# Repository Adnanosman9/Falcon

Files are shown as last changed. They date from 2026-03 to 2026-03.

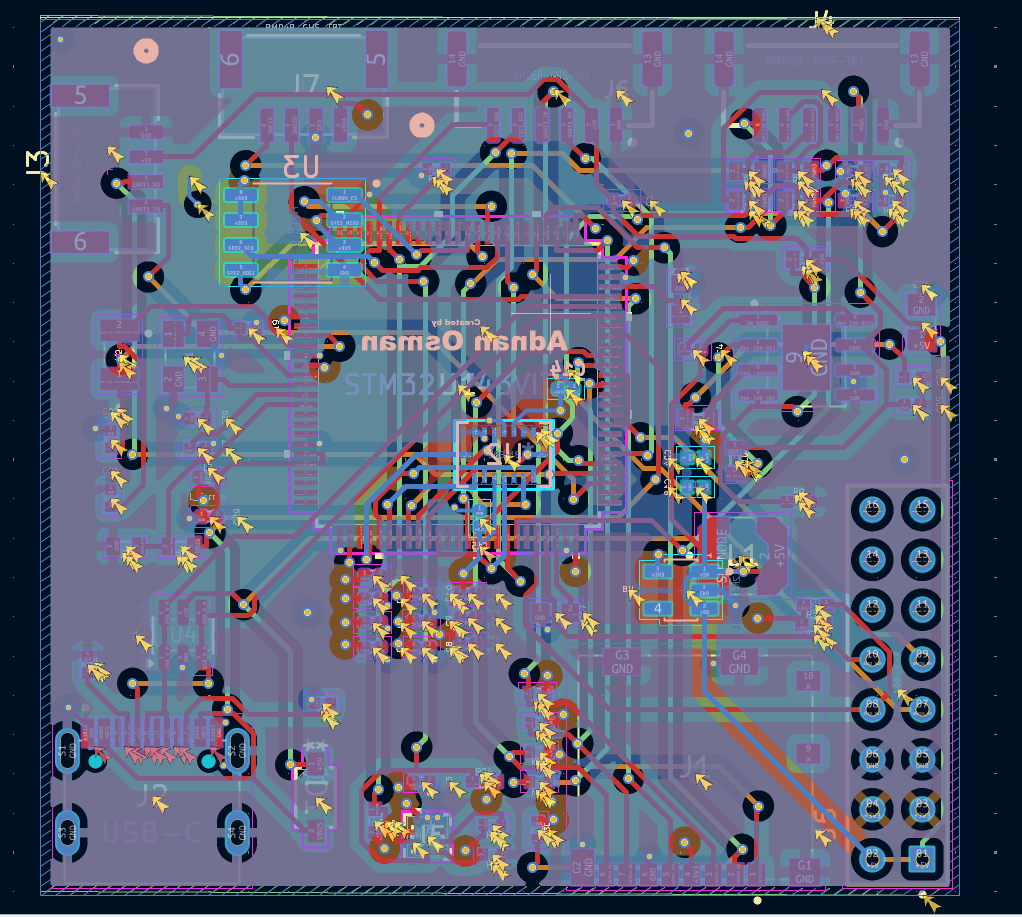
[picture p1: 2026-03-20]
Images/Screenshot 2026-03-19 203201.png

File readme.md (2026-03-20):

<h1 align="center">
  Falcon
  <br>
</h1>

<h4 align="center">
A custom flight controller built from scratch for a 3D surveying drone, running a custom port of ArduPilot
</h4>

<div align="center">





</div>

## Overview

I wanted to build a drone that could do proper 3D photogrammetry surveys. Off-the-shelf F4 flight controllers don't have enough processing power for the EKF configuration I need when fusing RTK GPS with IMU data at high rates. So I designed my own.

This is a flight controller built around the **STM32H743VIT6** , a 480MHz Cortex-M7 chip with 2MB flash and 1MB RAM. It runs a custom-compiled ArduPilot firmware with pin mappings specific to this board.

> ⚠️ PCB has not been manufactured yet. Firmware compiles and is ready to flash, but nothing has been tested on real hardware.

---

## Hardware Specs

| Component | Part |
| :--- | :--- |
| MCU | STM32H743VIT6 (480MHz, 2MB Flash) |
| IMU | BMI088 (6-axis, vibration-robust) |
| Barometer | BMP390 |
| Magnetometer | BMM350 |
| Flash Logging | FM25V02A (256KB FRAM) |
| SD Card | SDMMC1 4-bit interface |
| Power Input | MP1584EN buck → LP5907 3.3V LDO |
| USB | USB-C with USBLC6-2SC6 ESD protection |

---

## Why I Built It

I wanted to understand how flight controllers actually work, not just use one. Designing the schematic, figuring out why the VCAP pins need specific 2.2µF caps, getting the crystal load capacitors right, debugging the ArduPilot hwdef syntax , all of that taught me things I wouldn't have learned any other way.

Also, most hobbyist FCs are F4-based. The H7 gives me enough headroom to run ArduPilot's EKF3 with RTK GPS fusion without the processor struggling.

---

## How I Built It

### Schematic (KiCad)
- Designed the full power tree: LiPo → MP1584EN (5V buck) → LP5907 (3.3V LDO)
- VCAP1 and VCAP2 need exactly 2.2µF ceramic caps or the STM32H7 internal LDO becomes unstable, took a while to figure that out
- USB-C CC pins need 5.1kΩ pull-downs to GND or no charger recognizes the board as a device

### PCB Layout (KiCad)
- 4-layer board with bottom copper GND pour
- Crystal section has an isolated GND island underneath to avoid noise coupling into the oscillator
- DRC ended with 9 warnings, all on USB-C pad spacing (DRC settings issue, not a real problem). Zero footprint errors.

### Firmware (ArduPilot)
- Created a custom `hwdef.dat` that maps all STM32 pins to physical components: SPI for BMI088, I2C for BMP390 and BMM350, SDMMC1 for SD card, USART3 for GPS, PWM on TIM1
- Had to build a custom ChibiOS bootloader before the main firmware would compile
- Built on WSL (Ubuntu) using the `waf` build system and `arm-none-eabi-gcc`

---

## Current Status

- ✅ Schematic complete
- ✅ PCB layout complete, DRC clean
- ✅ Custom ArduPilot firmware builds successfully
- ⏳ PCB not manufactured yet
- ⏳ Not tested on real hardware

---

## How to Build Firmware

```bash
git clone --recurse-submodules https://github.com/ArduPilot/ardupilot.git
cd ardupilot
Tools/environment_install/install-prereqs-ubuntu.sh -y
. ~/.profile
mkdir libraries/AP_HAL_ChibiOS/hwdef/H7-DroneFC
cp Firmware/hwdef.dat libraries/AP_HAL_ChibiOS/hwdef/H7-DroneFC/
python Tools/scripts/build_bootloaders.py H7-DroneFC
./waf configure --board=H7-DroneFC
./waf copter
```

Output: `build/H7-DroneFC/bin/arducopter.bin`

---

## How to Flash

Connect an **ST-Link V2** to the SWD header:

| Header Pin | Signal |
| :--- | :--- |
| 1 | +3V3 |
| 2 | SWDIO (PA13) |
| 3 | SWCLK (PA14) |
| 4 | GND |

Flash `arducopter.bin` using STM32CubeProgrammer or Mission Planner (Load custom firmware).

---

## PWM Motor Outputs

| Output | MCU Pin | Timer |
| :--- | :--- | :--- |
| Motor 1 | PE9 | TIM1_CH1 |
| Motor 2 | PE11 | TIM1_CH2 |
| Motor 3 | PE13 | TIM1_CH3 |
| Motor 4 | PE14 | TIM1_CH4 |

---

## Repository Structure

```
H7-DroneFC/
├── PCB/     # KiCad schematic (.kicad_sch) and PCB layout (.kicad_pcb)
├── Firmware/     # hwdef.dat for ArduPilot custom board build
└── Images/       # Schematic screenshots and PCB renders
```

---

## ⚠️ Caution

Firmware has not been tested on real hardware yet. There may be issues with sensor initialization, SPI timing, or I2C addresses that only show up on actual hardware. Double check all pin assignments against the schematic before flashing and expect some debugging on first boot.

---

## Credits

- [ArduPilot](https://ardupilot.org/) for the open-source flight stack
- [KiCad](https://www.kicad.org/) for PCB design
- [Hack Club](https://hackclub.com/) for support

---

> GitHub [@Adnanosman9](https://github.com/Adnanosman9)

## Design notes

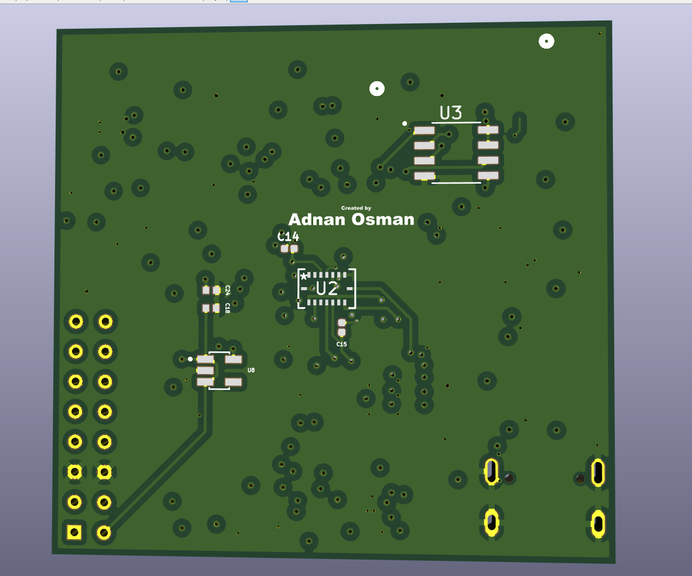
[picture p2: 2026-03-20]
Images/Screenshot 2026-03-19 203222.png

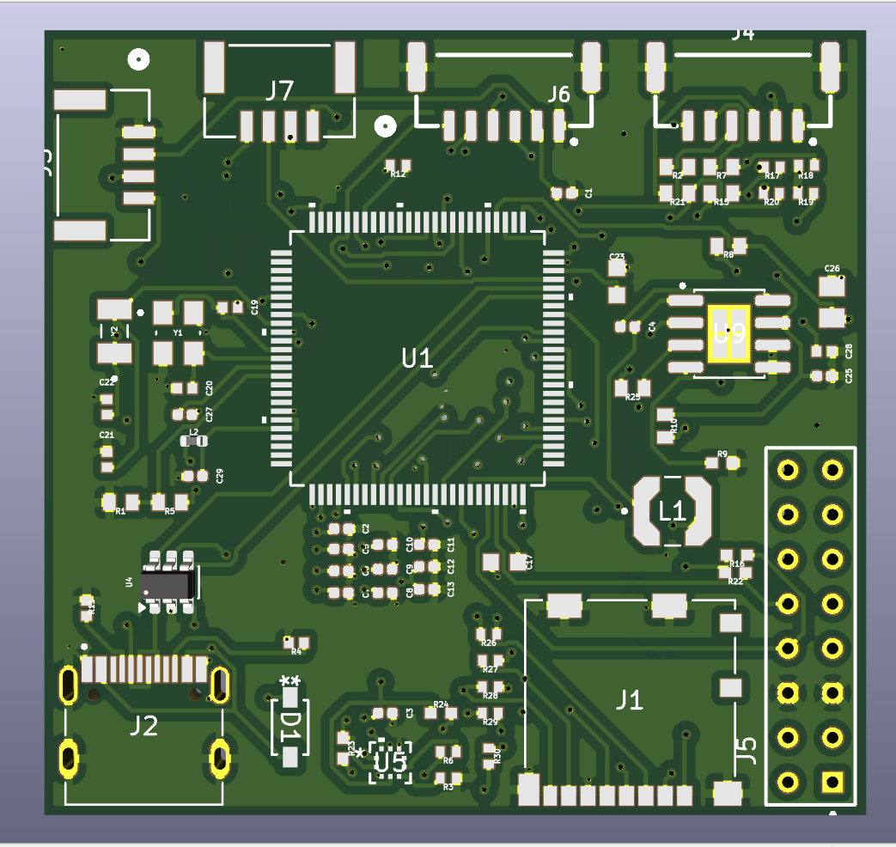
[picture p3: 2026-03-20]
Images/Screenshot 2026-03-19 203211.png

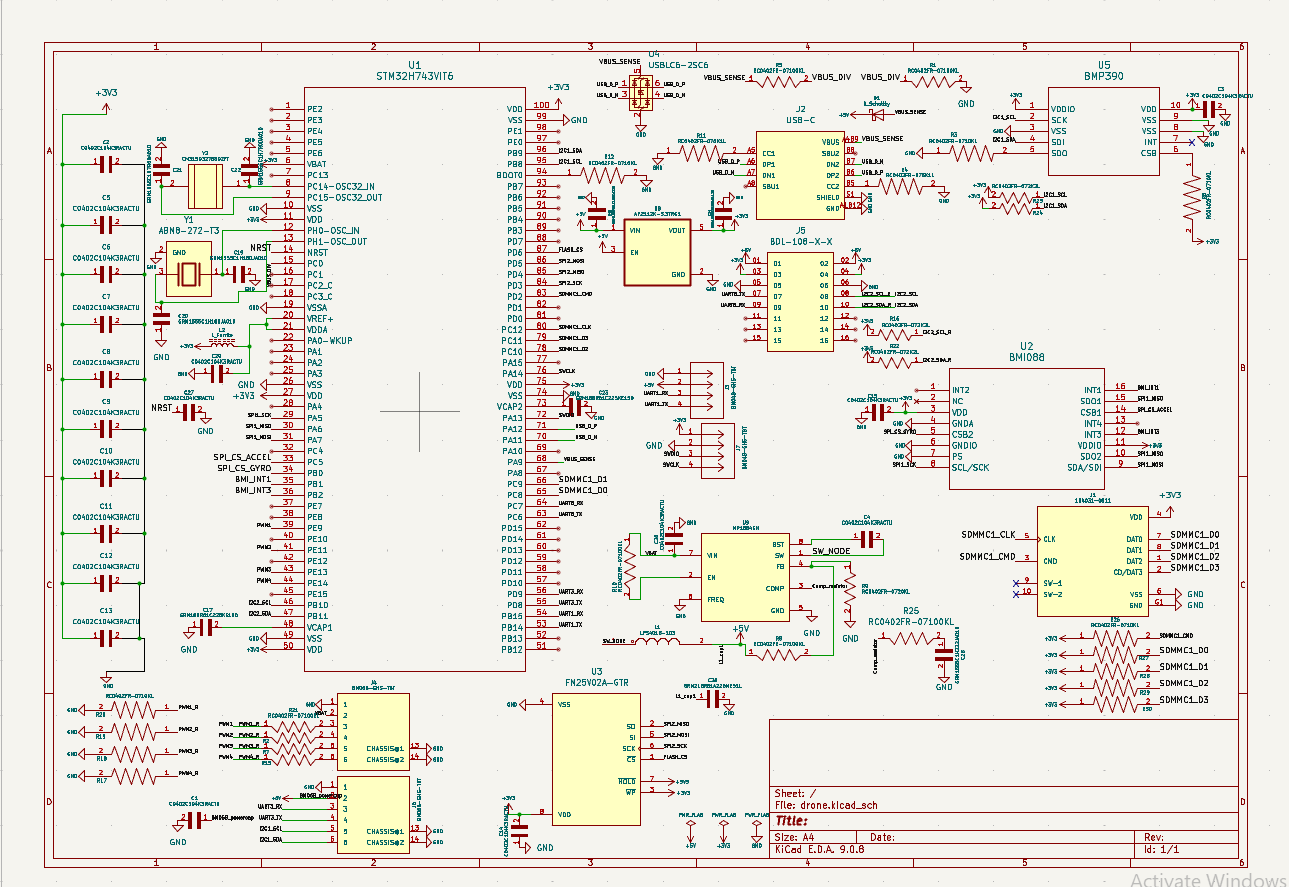
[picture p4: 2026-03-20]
Images/Screenshot 2026-03-19 203550.png

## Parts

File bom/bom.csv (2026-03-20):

 | References | Value | Footprint | Quantity
1 | C1, C2, C3, C4, C5, C6, C7, C8, C9, C10, C11, C12, C13, C14, C15, C25, C27, C29 | C0402C104K3RACTU | CAPC1005X55N | 18
2 | C17, C23 | GRM188R61C225KE15D | CAPC1608X90N | 2
3 | C18, C24 | GRM155R61E105KA12D | CAPC1005X55N | 2
4 | C19, C20 | GRM1555C1H180JA01D | CAPC1005X55N | 2
5 | C21, C22 | GRM1555C1H7R0DA01D | CAPC1005X55N | 2
6 | C26 | GRM21BR61A226ME51L | CAPC2012X140N | 1
7 | C28 | GRM1555C1H222JA01D | CAPC1005X55N | 1
8 | R3, R6, R12, R17, R18, R19, R20, R26, R27, R28, R29, R30 | RC0402FR-0710KL | RESC1005X40N | 12
9 | R1, R5, R8, R10, R25 | RC0402FR-07100KL | RESC1005X40 | 5
10 | R2, R7, R15, R21 | RC0402FR-07100RL | RESC1005X40 | 4
11 | R16, R22, R23, R24 | RC0402FR-072K2L | RESC1005X40N | 4
12 | R4, R11 | RC0402FR-075K1L | RESC1005X40N | 2
13 | R9 | RC0402FR-0720KL | RESC1005X40N | 1
14 | L1 | LPS4018-103 | IND_LPS4018-103 | 1
15 | L2 | L_Ferrite | L_0402_1005Metric | 1
16 | D1 | D_Schottky | SDO_SOD-123_MCC | 1
17 | U1 | STM32H743VIT6 | LQFP100-14x14mm | 1
18 | U2 | BMI088 | QFN_BMI085_BOS | 1
19 | U3 | FM25V02A-GTR | SOIC127P602X172-8N | 1
20 | U4 | USBLC6-2SC6 | SOT-23-6 | 1
21 | U5 | BMP390 | 10LGA_2X2X0p75_BOS | 1
22 | U8 | AP2112K-3.3TRG1 | SOT95P285X140-5N | 1
23 | U9 | MP1584EN | SOIC127P600X170-9N | 1
24 | Y1 | ABM8-272-T3 | XTAL_ABM8-272-T3 | 1
25 | Y2 | CM315D32768DZFT | XTAL_CM315D32768DZFT | 1
26 | J3, J7 | BM04B-GHS-TBT | CONN_BM04B-GHS-TBT_JST | 2
27 | J4, J6 | BM06B-GHS-TBT | BM06B-GHS-TBT | 2
28 | J1 | 104031-0811 | MOLEX_104031-0811 | 1
29 | J2 | USB-C | HRO_TYPE-C-31-M-12 | 1
30 | J5 | BDL-108-X-X | SAMTEC_BDL-108-X-X | 1

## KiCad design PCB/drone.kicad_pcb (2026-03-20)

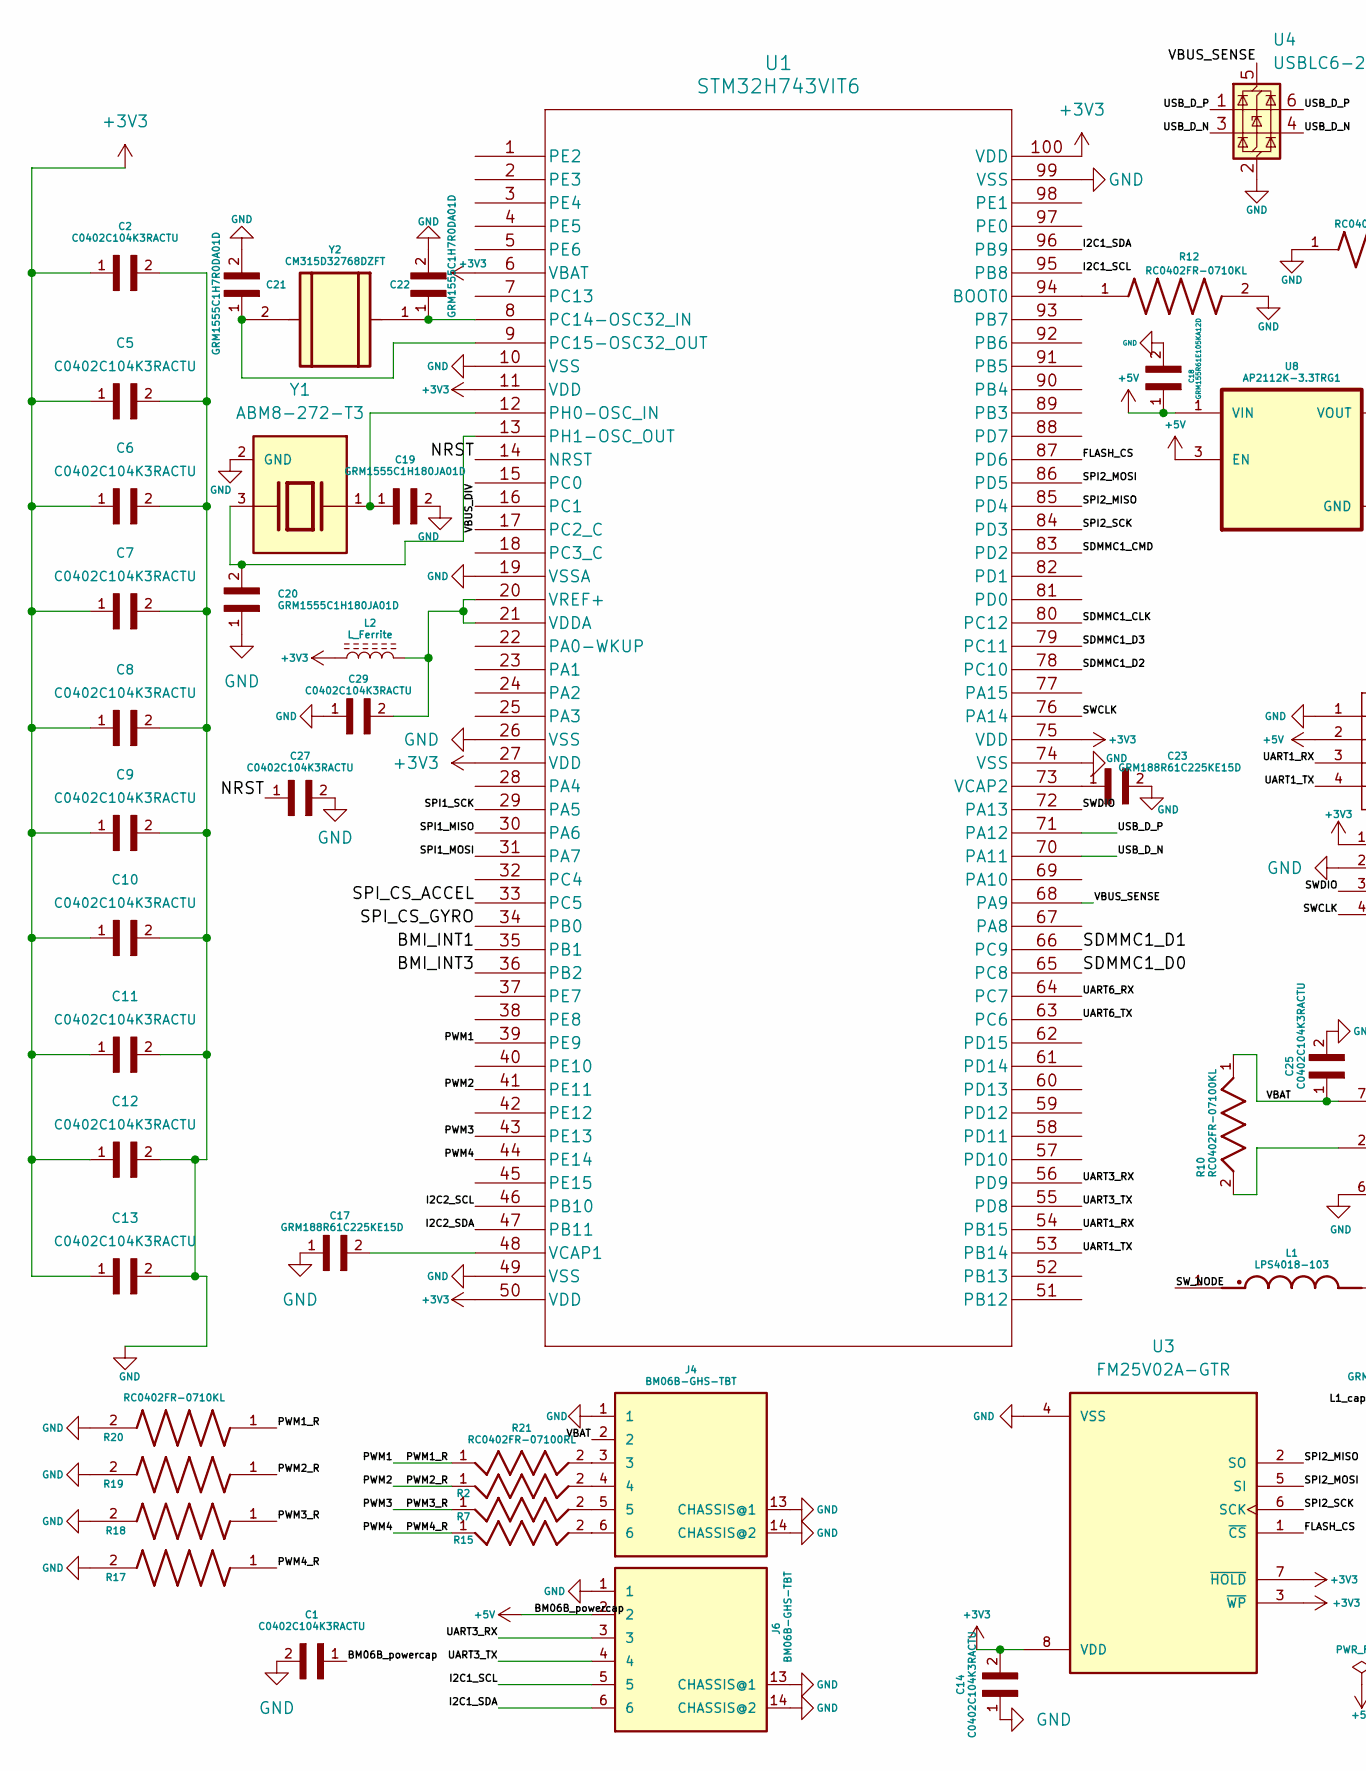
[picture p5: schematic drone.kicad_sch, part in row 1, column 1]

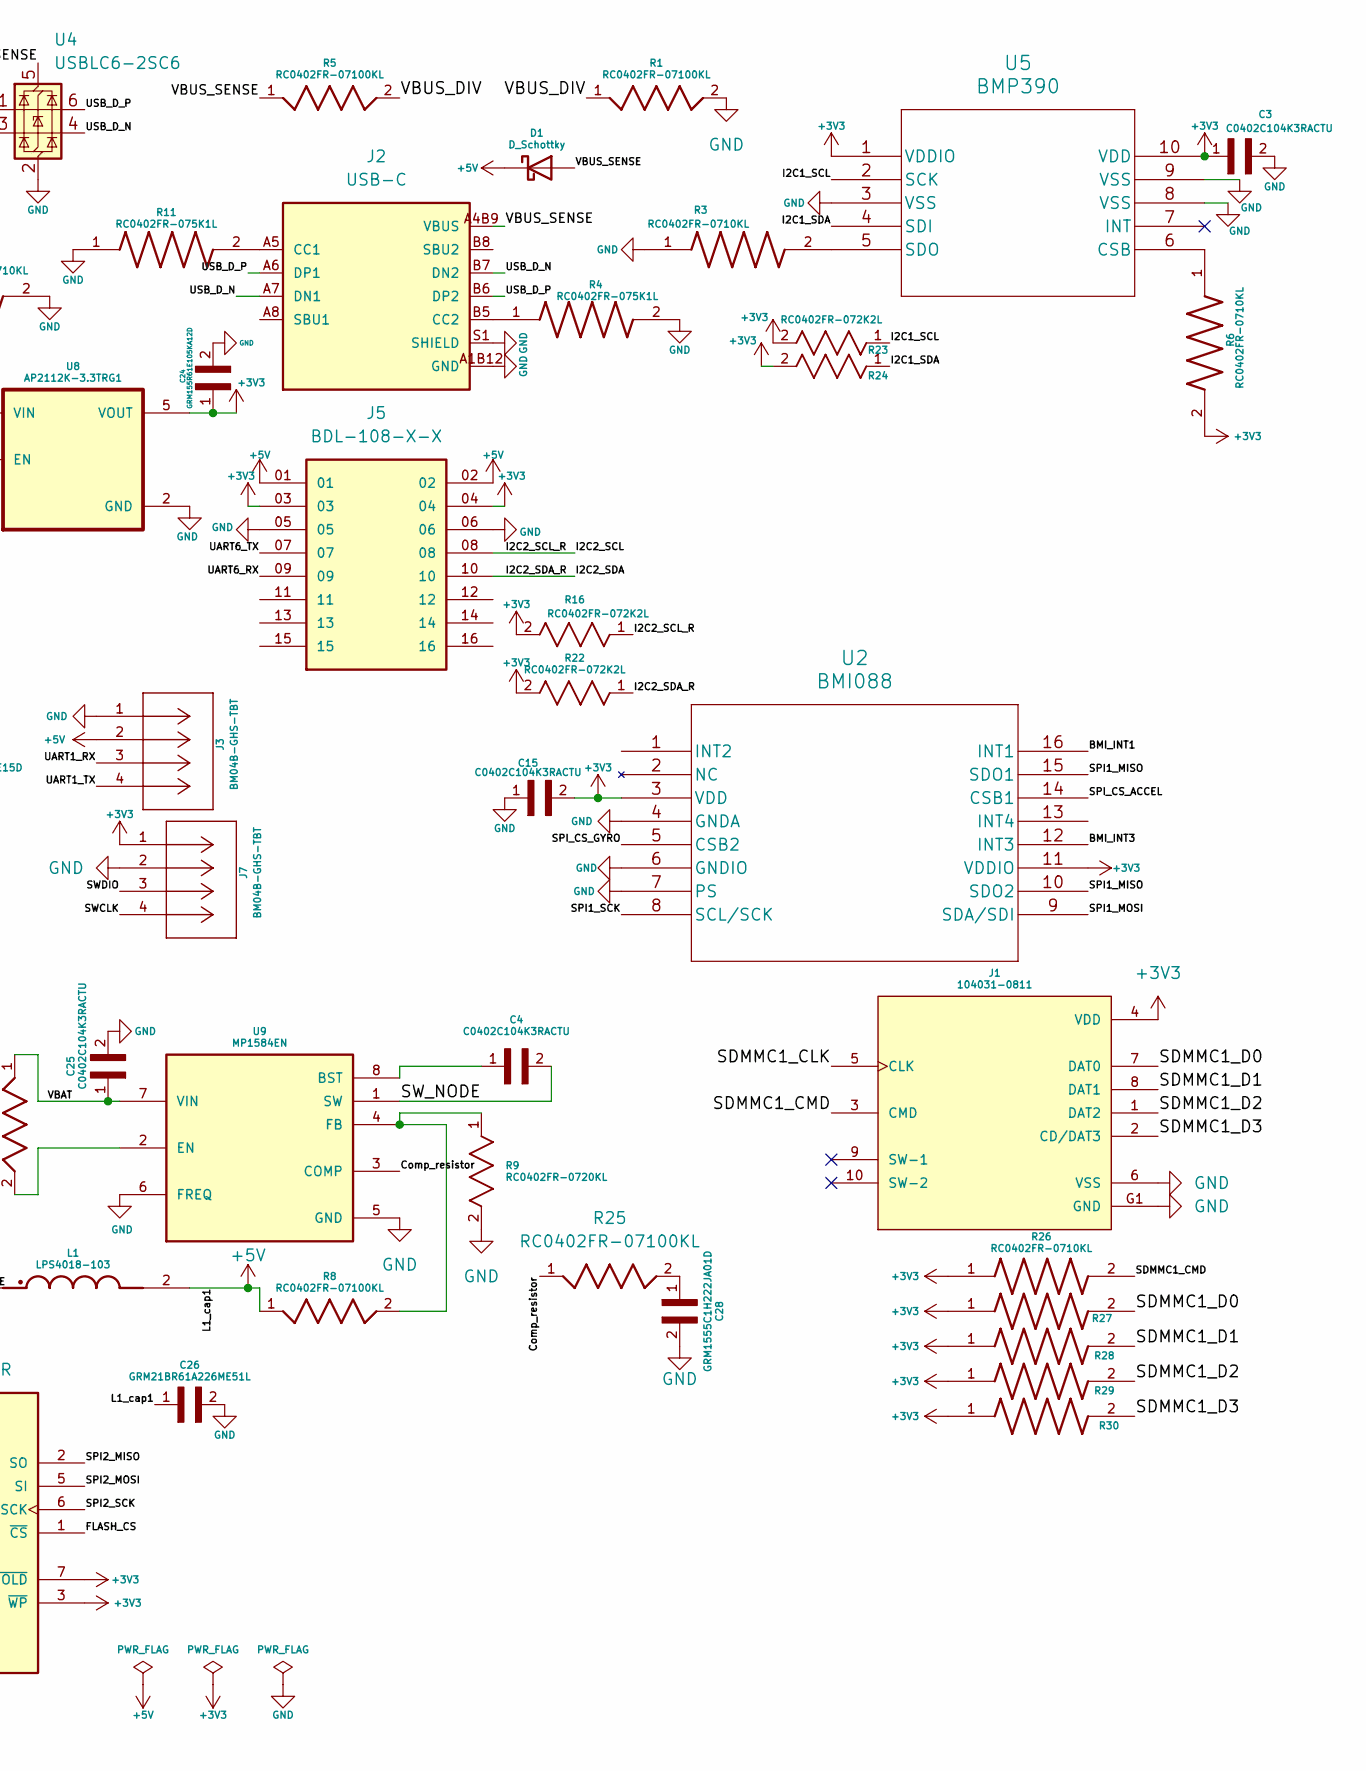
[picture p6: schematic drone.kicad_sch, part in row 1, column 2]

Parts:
C1, C2, C3, C4, C5, C6, C7, C8, C9, C10, C11, C12, C13, C14, C15, C25, C27, C29: C0402C104K3RACTU; CAPC1005X55N; PARTREV N/A
C17, C23: GRM188R61C225KE15D; CAPC1608X90N
C18, C24: GRM155R61E105KA12D; CAPC1005X55N
C19, C20: GRM1555C1H180JA01D; CAPC1005X55N
C21, C22: GRM1555C1H7R0DA01D; CAPC1005X55N; DigiKey_Part_Number 490-5878-1-ND
C26: GRM21BR61A226ME51L; CAPC2012X140N
C28: GRM1555C1H222JA01D; CAPC1005X55N
D1: D_Schottky; SDO_SOD-123_MCC
J1: 104031-0811; MOLEX_104031-0811; PARTREV B2
J2: USB-C; HRO_TYPE-C-31-M-12; LCSCPART# C165948
J3, J7: BM04B-GHS-TBT; CONN_BM04B-GHS-TBT_JST; MANUFACTURER_PART_NUMBER BM04B-GHS-TBT
J4, J6: BM06B-GHS-TBT
J5: BDL-108-X-X; SAMTEC_BDL-108-X-X; PARTREV A
L1: LPS4018-103; IND_LPS4018-103; PARTREV 02/23/22
L2: L_Ferrite; L_0402_1005Metric
R1, R5, R8, R10, R25: RC0402FR-07100KL; RESC1005X40
R2, R7, R15, R21: RC0402FR-07100RL; RESC1005X40
R3, R6, R12, R17, R18, R19, R20, R26, R27, R28, R29, R30: RC0402FR-0710KL; RESC1005X40N; PARTREV V.12
R4, R11: RC0402FR-075K1L; RESC1005X40N
R9: RC0402FR-0720KL; RESC1005X40N; TOLERANCE ±1%; MPN RC0402FR-0720KL
R16, R22, R23, R24: RC0402FR-072K2L; RESC1005X40N; TOLERANCE ±1%; MPN RC0402FR-072K2L
U1: STM32H743VIT6; LQFP100-14x14mm
U2: BMI088; QFN_BMI085_BOS
U3: FM25V02A-GTR; SOIC127P602X172-8N
U4: USBLC6-2SC6; SOT-23-6
U5: BMP390; 10LGA_2X2X0p75_BOS
U8: AP2112K-3.3TRG1; SOT95P285X140-5N; PARTREV 2-2
U9: MP1584EN; SOIC127P600X170-9N
Y1: ABM8-272-T3; XTAL_ABM8-272-T3; PARTREV 07-29-20
Y2: CM315D32768DZFT; XTAL_CM315D32768DZFT

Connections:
+3V3: C2.1, C3.1, C5.1, C6.1, C7.1, C8.1, C9.1, C10.1, C11.1, C12.1, C13.1, C14.2, C15.2, C24.1, J1.4 (VDD), J5.03, J5.04, J7.1, L2.1, R6.2, R16.2, R22.2, R23.2, R24.2, R26.1, R27.1, R28.1, R29.1, R30.1, U1.6 (VBAT), U1.11 (VDD), U1.27 (VDD), U1.50 (VDD), U1.75 (VDD), U1.100 (VDD), U2.3 (VDD), U2.11 (VDDIO), U3.3 (~WP), U3.7 (~HOLD), U3.8 (VDD), U5.1 (VDDIO), U5.10 (VDD), U8.5 (VOUT)
/BMI_INT1: U1.35 (PB1), U2.16 (INT1)
/BMI_INT3: U1.36 (PB2), U2.12 (INT3)
/Comp_resistor: R25.1, U9.3 (COMP)
/FLASH_CS: U1.87 (PD6), U3.1 (~CS)
/I2C1_SCL: J6.5, R23.1, U1.95 (PB8), U5.2 (SCK)
/I2C1_SDA: J6.6, R24.1, U1.96 (PB9), U5.4 (SDI)
/I2C2_SCL: J5.08, R16.1, U1.46 (PB10)
/I2C2_SDA: J5.10, R22.1, U1.47 (PB11)
/NRST: C27.1, U1.14 (NRST)
/PWM1: R20.1, R21.1, U1.39 (PE9)
/PWM2: R2.1, R19.1, U1.41 (PE11)
/PWM3: R7.1, R18.1, U1.43 (PE13)
/PWM4: R15.1, R17.1, U1.44 (PE14)
/SDMMC1_CLK: J1.5 (CLK), U1.80 (PC12)
/SDMMC1_CMD: J1.3 (CMD), R26.2, U1.83 (PD2)
/SDMMC1_D0: J1.7 (DAT0), R27.2, U1.65 (PC8)
/SDMMC1_D1: J1.8 (DAT1), R28.2, U1.66 (PC9)
/SDMMC1_D2: J1.1 (DAT2), R29.2, U1.78 (PC10)
/SDMMC1_D3: J1.2 (CD/DAT3), R30.2, U1.79 (PC11)
/SPI1_MISO: U1.30 (PA6), U2.10 (SDO2), U2.15 (SDO1)
/SPI1_MOSI: U1.31 (PA7), U2.9 (SDA/SDI)
/SPI1_SCK: U1.29 (PA5), U2.8 (SCL/SCK)
/SPI2_MISO: U1.85 (PD4), U3.2 (SO)
/SPI2_MOSI: U1.86 (PD5), U3.5 (SI)
/SPI2_SCK: U1.84 (PD3), U3.6 (SCK)
/SPI_CS_ACCEL: U1.33 (PC5), U2.14 (CSB1)
/SPI_CS_GYRO: U1.34 (PB0), U2.5 (CSB2)
/SWCLK: J7.4, U1.76 (PA14)
/SWDIO: J7.3, U1.72 (PA13)
/SW_NODE: C4.2, L1.1, U9.1 (SW)
/UART1_RX: J3.3, U1.54 (PB15)
/UART1_TX: J3.4, U1.53 (PB14)
/UART3_RX: J6.3, U1.56 (PD9)
/UART3_TX: J6.4, U1.55 (PD8)
/UART6_RX: J5.09, U1.64 (PC7)
/UART6_TX: J5.07, U1.63 (PC6)
/USB_D_N: J2.A7 (DN1), J2.B7 (DN2), U1.70 (PA11), U4.3 (I/O2), U4.4 (I/O2)
/USB_D_P: J2.A6 (DP1), J2.B6 (DP2), U1.71 (PA12), U4.1 (I/O1), U4.6 (I/O1)
/VBAT: C25.1, J4.2, R10.1, U9.7 (VIN)
/VBUS_DIV: R1.1, R5.2, U1.15 (PC0)
GND: C1.2, C2.2, C3.2, C5.2, C6.2, C7.2, C8.2, C9.2, C10.2, C11.2, C12.2, C13.2, C14.1, C15.1, C17.1, C18.2, C19.2, C20.1, C21.2, C22.2, C23.2, C24.2, C25.2, C26.2, C27.2, C28.2, C29.1, J1.6 (VSS), J1.G1 (GND), J1.G2 (GND), J1.G3 (GND), J1.G4 (GND), J2.A1B12 (GND), J2.B1A12 (GND), J2.S1 (SHIELD), J2.S2 (SHIELD), J2.S3 (SHIELD), J2.S4 (SHIELD), J3.1, J4.1, J4.13 (CHASSIS@1), J4.14 (CHASSIS@2), J5.05, J5.06, J6.1, J6.13 (CHASSIS@1), J6.14 (CHASSIS@2), J7.2, R1.2, R3.1, R4.2, R9.2, R11.1, R12.2, R17.2, R18.2, R19.2, R20.2, U1.10 (VSS), U1.19 (VSSA), U1.26 (VSS), U1.49 (VSS), U1.74 (VSS), U1.99 (VSS), U2.4 (GNDA), U2.6 (GNDIO), U2.7 (PS), U3.4 (VSS), U4.2 (GND), U5.3 (VSS), U5.8 (VSS), U5.9 (VSS), U8.2 (GND), U9.5 (GND), U9.6 (FREQ), U9.9 (GND), Y1.2 (GND), Y1.4 (GND)
unnamed: C28.1, R25.2
unnamed: J2.A5 (CC1), R11.2
unnamed: J2.B5 (CC2), R4.1
unnamed: J4.3, R21.2
unnamed: J4.4, R2.2
unnamed: J4.5, R7.2
unnamed: J4.6, R15.2
unnamed: R12.1, U1.94 (BOOT0)
unnamed: C22.1, U1.8 (PC14-OSC32_IN), Y2.1
unnamed: C21.1, U1.9 (PC15-OSC32_OUT), Y2.2
unnamed: C19.1, U1.12 (PH0-OSC_IN), Y1.1
unnamed: C20.2, U1.13 (PH1-OSC_OUT), Y1.3
unnamed: C17.2, U1.48 (VCAP1)
unnamed: C23.1, U1.73 (VCAP2)
unnamed: C29.2, L2.2, U1.20 (VREF+), U1.21 (VDDA)
unnamed: R6.1, U5.6 (CSB)
unnamed: R3.2, U5.5 (SDO)
unnamed: C4.1, U9.8 (BST)
unnamed: R10.2, U9.2 (EN)
unnamed: R8.2, R9.1, U9.4 (FB)

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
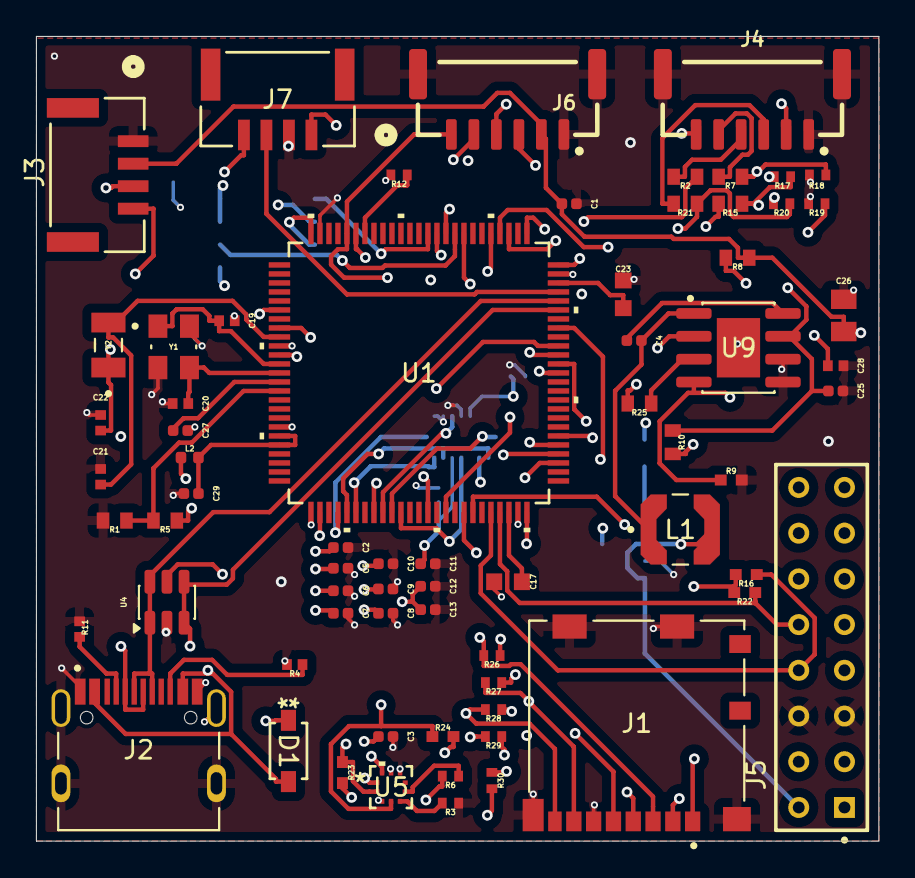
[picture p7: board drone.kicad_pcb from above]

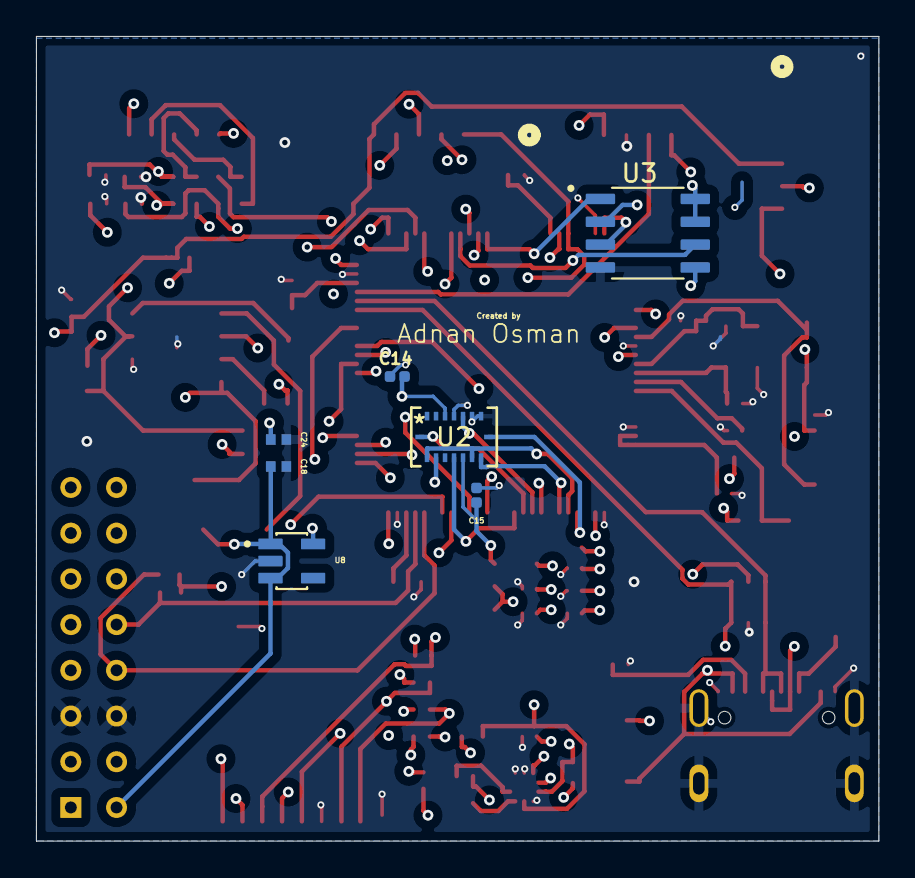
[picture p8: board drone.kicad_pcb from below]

Board: 4 copper layers, 46.8 x 44.7 mm, 75 parts (7 on the bottom side), 64 nets.

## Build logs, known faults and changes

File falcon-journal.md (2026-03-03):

<!--
  This journal is auto generated by Hack Club Blueprint.
-->

# 3/3/2026 3 PM - Project Genesis & Strategic Pivot  

_Time spent: 1.0h_  

## **Pre planning**
**I’m building a custom 3D-surveying drone from scratch.**
I mean actual PCB, frame, suffering.

Currently working on the flight Controller. 
I have decided to make this FC on KICAD
And maybe I will be using Fusion 360 for other parts.

Basically, I’m choosing the hardest possible route instead of buying a Pixhawk like a normal person.

I am not sure if it will work in 1st attempt, But if it works?
It’s going to be insane.

### A basic pre planning and list on paper 


# 3/3/2026 5 PM - Choosing the Brain and the Inner Ear  

_Time spent: 1.0h_  

I have choosen `STM32H743VIT6` as the main MCU for my FC as STM32H7 is basically the gold standard in modern UAVs. 

> **Sensors**
> IMU - `BMI088`
> Barometer - `BMP390`
> Compass - `BMM350`
> Buck Converter - `MP1584EN`
> LDO - `AP2112K`
> Power connector - `USB-C`

Basic mandetory sensors are done, Now it's time for the hardest process of calculation to add resistor and capacitors. 



> Next part requires Physics calculation so I am going to take my nightmare sorry, **NOTEBOOK**   

# 3/4/2026 - Schematic Assembly  

_Time spent: 3.0h_  

After doing calculations, I’m back to actually building the schematic.

I’m not importing everything at once because that will create symbol conflicts, footprint mismatches, and ERC errors. So I’m gdoing one block at a time. 

> **Check list**
> MCU
> Sensors
> Power Section
> Safety Resistors and savior Capacitors

_Not everything is imported yet because KiCad’s default sheet size feels tiny compared Flight controller schematic._



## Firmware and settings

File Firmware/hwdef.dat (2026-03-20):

# Custom STM32H743VIT6 Flight Controller
# Board by Adnan

# MCU Type
MCU STM32H743xx STM32H743xx

# Board ID (using MatekH743 base ID)
APJ_BOARD_ID 1013

# Crystal: 8MHz
OSCILLATOR_HZ 8000000

# Flash size
FLASH_SIZE_KB 2048
FLASH_RESERVE_START_KB 128
define HAVE_FASTRAM_REGION 1

# USB
PA11 OTG_FS_DM OTG1
PA12 OTG_FS_DP OTG1

# --- POWER SENSE ---
PA8 VBUS INPUT OPENDRAIN
PC0 BATT_VOLTAGE_SENS ADC1 SCALE(1)

# --- SPI1 (BMI088 IMU) ---
PA5 SPI1_SCK SPI1
PA6 SPI1_MISO SPI1
PA7 SPI1_MOSI SPI1
PC4 BMI088_CS_ACCEL CS
PC5 BMI088_CS_GYRO CS

# BMI088 Interrupts
PC1 BMI088_INT1 INPUT
PB1 BMI088_INT3 INPUT

# --- I2C1 (BMP390 Barometer + BMM350 Magnetometer) ---
I2C_ORDER I2C1
PB8 I2C1_SCL I2C1
PB9 I2C1_SDA I2C1

# BMP390 Interrupt
PB2 BMP390_INT INPUT

# --- SPI3 (FM25V02A FRAM Dataflash) ---
PB3 SPI3_SCK SPI3
PB4 SPI3_MISO SPI3
PB5 SPI3_MOSI SPI3
PD6 FLASH_CS CS

# --- SDMMC1 (SD Card) ---
PC8  SDMMC1_D0 SDMMC1
PC9  SDMMC1_D1 SDMMC1
PC10 SDMMC1_D2 SDMMC1
PC11 SDMMC1_D3 SDMMC1
PC12 SDMMC1_CK SDMMC1
PD2  SDMMC1_CMD SDMMC1

# --- MOTOR PWM OUTPUTS (TIM1) ---
PE9  TIM1_CH1 TIM1 PWM(1) GPIO(50)
PE11 TIM1_CH2 TIM1 PWM(2) GPIO(51)
PE13 TIM1_CH3 TIM1 PWM(3) GPIO(52)
PE14 TIM1_CH4 TIM1 PWM(4) GPIO(53)

# --- GPS / SERIAL3 (UART3) ---
PD8 USART3_TX USART3
PD9 USART3_RX USART3

# --- SERIAL CONFIG ---
SERIAL_ORDER OTG1 USART3

# --- DEVICE DRIVERS ---
SPIDEV bmi088_accel SPI1 DEVID1 BMI088_CS_ACCEL MODE3 1*MHZ 4*MHZ
SPIDEV bmi088_gyro  SPI1 DEVID2 BMI088_CS_GYRO  MODE3 1*MHZ 4*MHZ

IMU BMI088 SPI:bmi088_accel SPI:bmi088_gyro ROTATION_NONE

BARO BMP280 I2C:0:0x76

define AP_COMPASS_PROBING_ENABLED 1
define HAL_COMPASS_AUTO_ROT_DEFAULT 2

# --- STORAGE ---
STORAGE_FLASH_PAGE 14
define HAL_STORAGE_SIZE 32768

# --- DEFAULT PARAMETERS ---
define HAL_BATT_VOLT_PIN 10
define HAL_BATT_VOLT_SCALE 11.0

# --- HEAP ---
define HAL_WITH_DSP 1
define HAL_NUMCAN_IFACES 0

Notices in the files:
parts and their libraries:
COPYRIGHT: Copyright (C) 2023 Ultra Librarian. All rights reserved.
